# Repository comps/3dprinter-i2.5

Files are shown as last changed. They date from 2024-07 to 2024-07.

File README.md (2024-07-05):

# The i2.5 ("Tiny") 3D printer

This was a learning project of mine on how to design and build a moving-bed
style 3D printer from scratch.

It started in ~2017 and grew in time and money spent from there, with me trying
various "new technologies" on the always-work-in-progress printer.

Things like

- sliding IGUS bushings instead of LM8UU bearings
- graphite-based self-lubricating brass bushings instead of LM8UU
- grease types on the Z-axis screw (dry graphite/teflon, calcium sulfonate,
  etc.)
- belt tensioning systems (and various types of timing belt fiber
  reinforcements)
- Z-axis screw couplers and their (in)accuracy
- bed probing (the design has left-over space for an X-gantry-mounted
  limit switch probe, the real printer ended up using an X-carriage
  inductive probe)
- inductive probe options and failure modes (~4 variants, sensors randomly
  failing due to 60C heat from the bed)
- magnetic beds and their limitations (tried 2-3 variants, some DIY,
  some purchased)
  - ended up using bed clamps as discrete magnets (glued to underside)
    were never strong enough to prevent the steel sheet from moving
  - sourcing spring steel sheets was also near-impossible in 2019
- heated bed issues (tried PCB, which flexed too much, tried fixing
  aluminium heatbed with broken corners, reliability issues, etc.)
  - also several variations on bed springs (stiffness, types, ended up
    with silicone-based springs)
- electronics
  - started as 8-bit, two different boards, using custom wiring
    for TMC2130 back when it was bleeding-edge and only Prusa had it
  - added an 8x8 red LED matrix to show gcode command queue
  - developed custom Blue Pill based stack for a 32bit cut-down Marlin 2.0
  - switched to a stock imported 32bit board later on
- extruder was originally a custom design loosely based on Greg's Wade's
  geared extruder using E3D V6, then re-worked to use E3D Titan Aero heatsink,
  then abandoned for a stock E3D Titan Aero extruder
  - with a custom-modified NEMA17 motor to use a longer shaft, so it can be
    mounted through the X-carriage, distributing front/back weight

Ultimately, the scope and cost of the project ended up being about 10x of what
it was originally meant to be, mainly thanks to unreliable, out-of-spec and
otherwise broken parts from Ebay and Aliexpress.  
(Bearings binding, bushings with wrong hole tolerances, electronics randomly
failing, IC chips like CH340 randomly locking up, toothed gears for driving
filament being made of soft metal, GT2 pulleys with malformed teeth, etc., etc.)

This repository therefore serves mainly as a source of spare parts for the one
printer that was ever built.

Please don't build another one, there are many better options these days.  
It's not 2017 anymore.

---

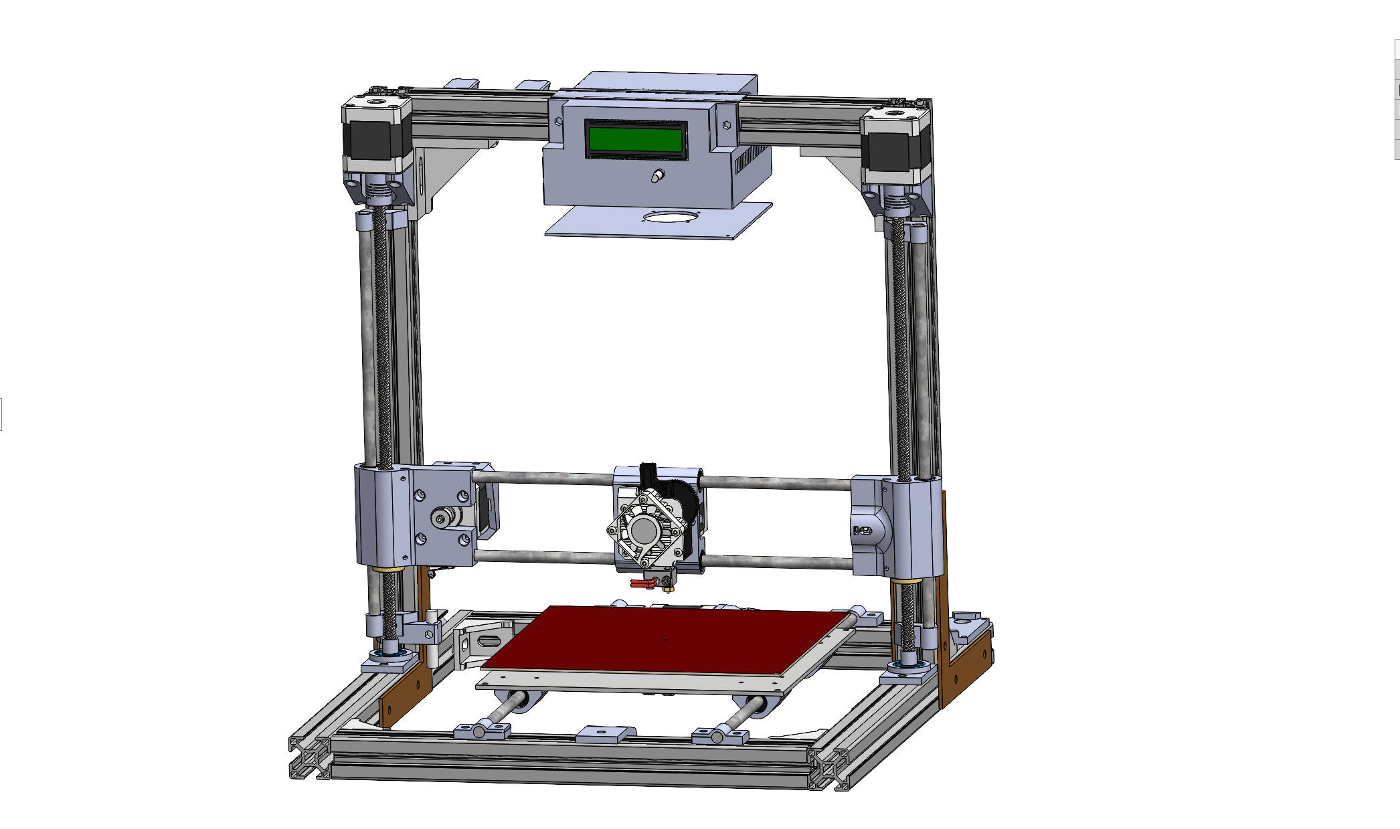
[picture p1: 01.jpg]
front overview

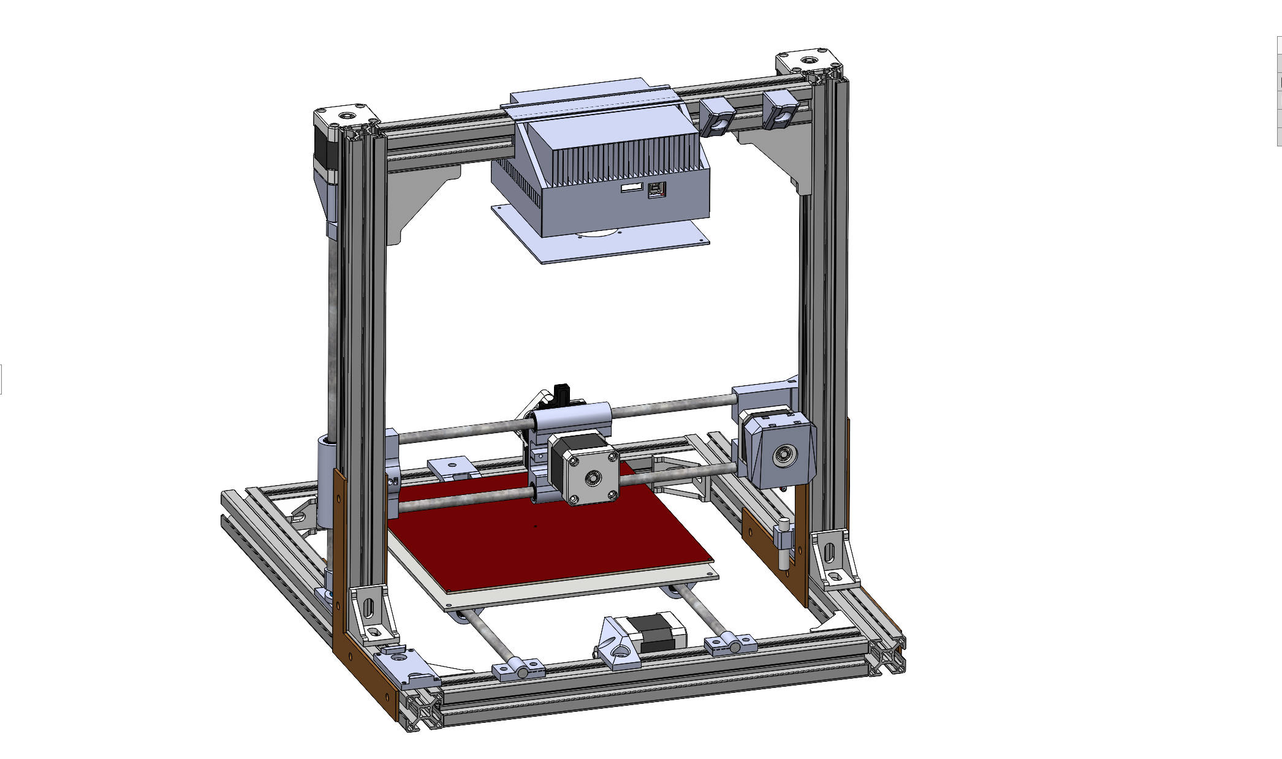
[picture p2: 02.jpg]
back overview

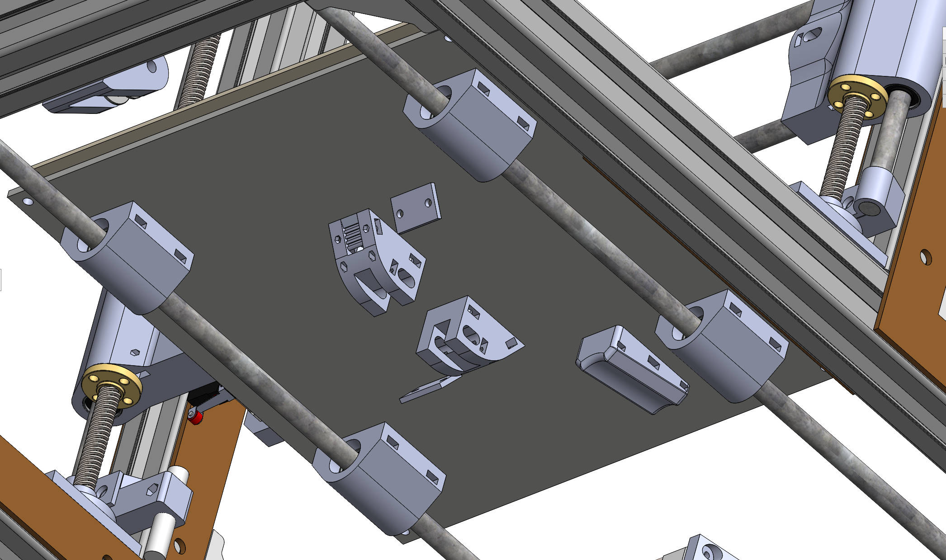
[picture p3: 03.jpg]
underside


---

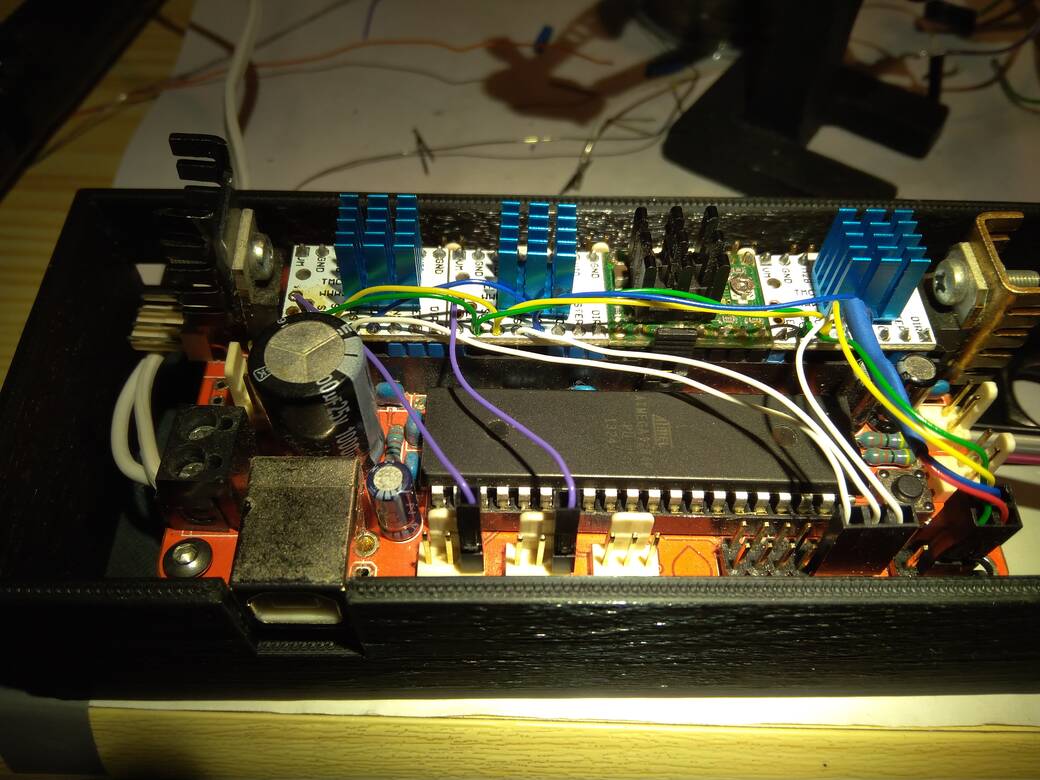
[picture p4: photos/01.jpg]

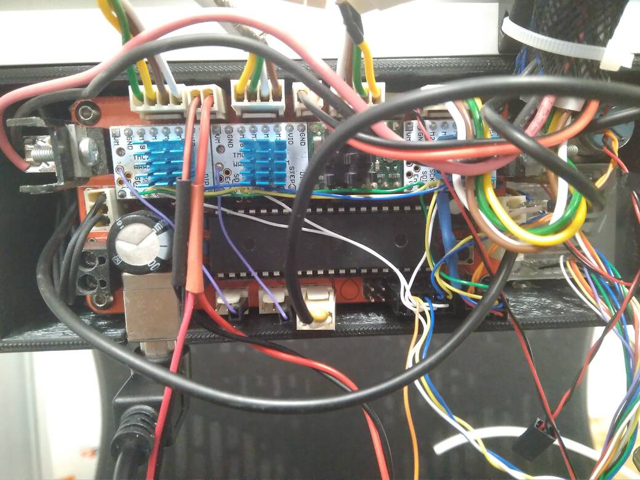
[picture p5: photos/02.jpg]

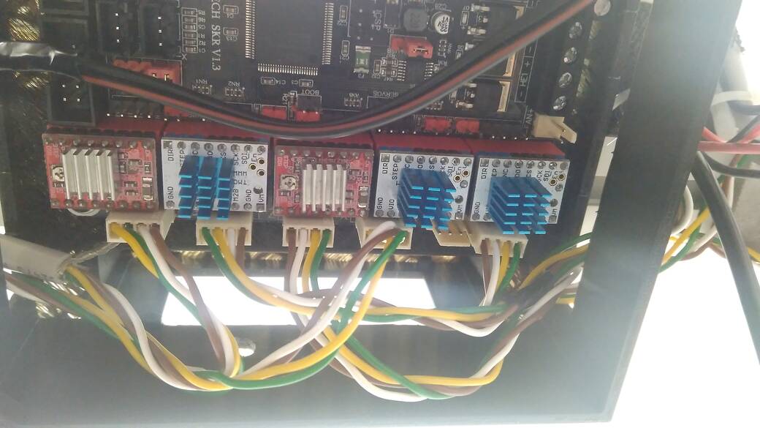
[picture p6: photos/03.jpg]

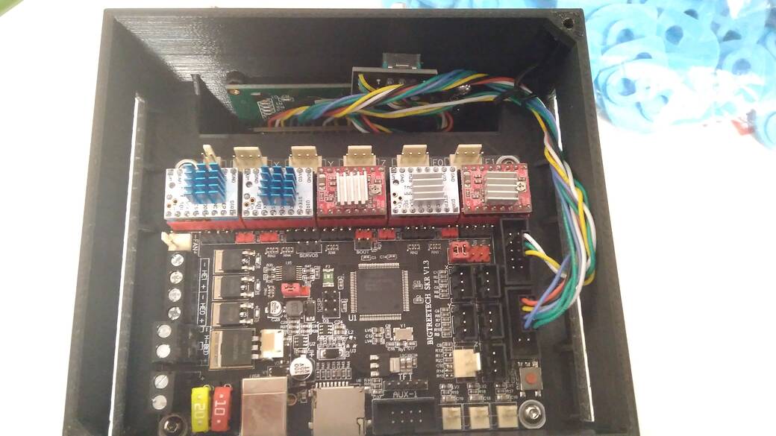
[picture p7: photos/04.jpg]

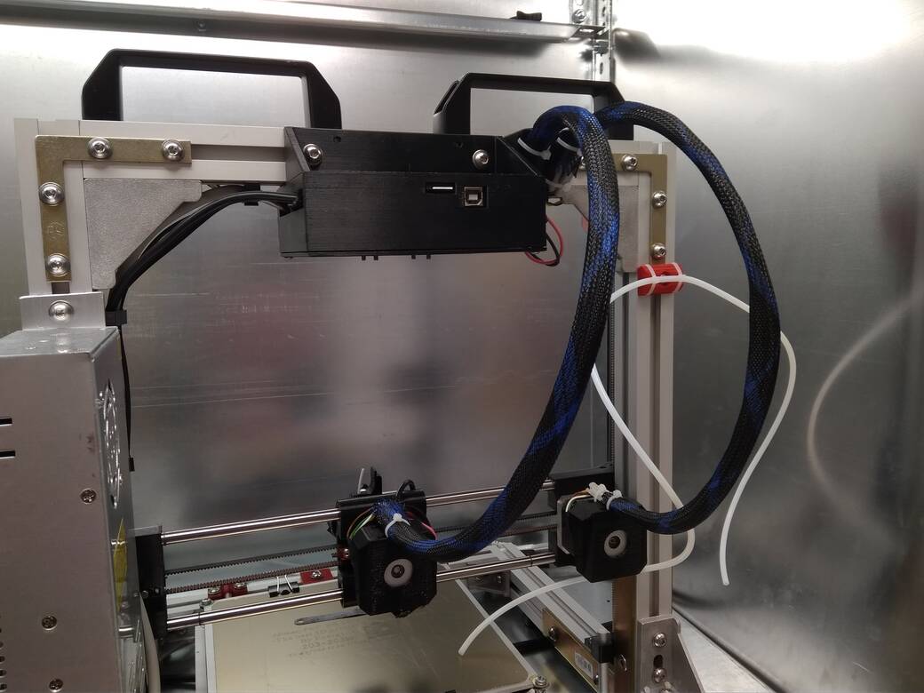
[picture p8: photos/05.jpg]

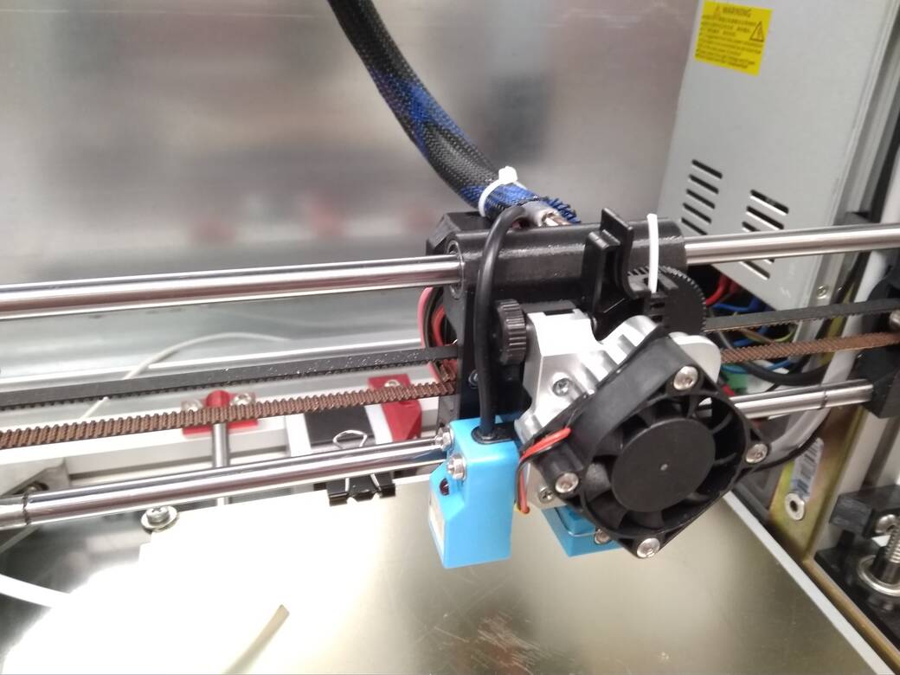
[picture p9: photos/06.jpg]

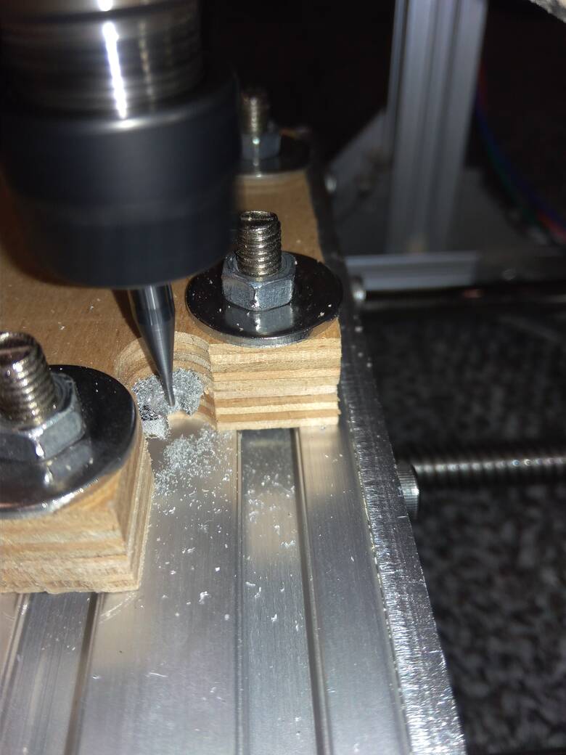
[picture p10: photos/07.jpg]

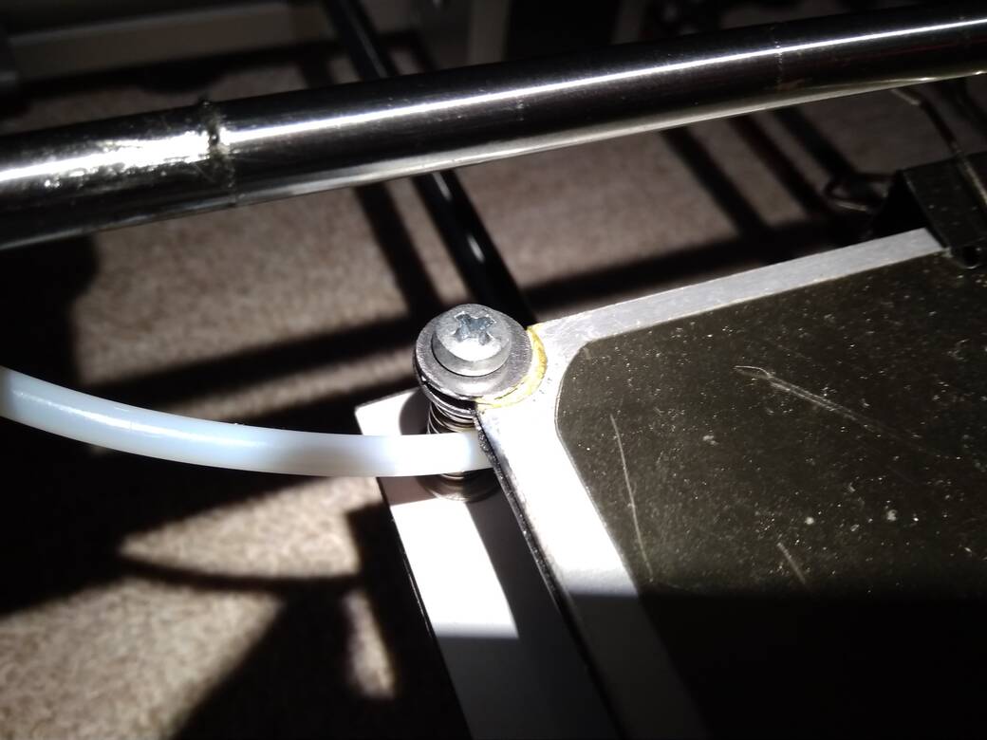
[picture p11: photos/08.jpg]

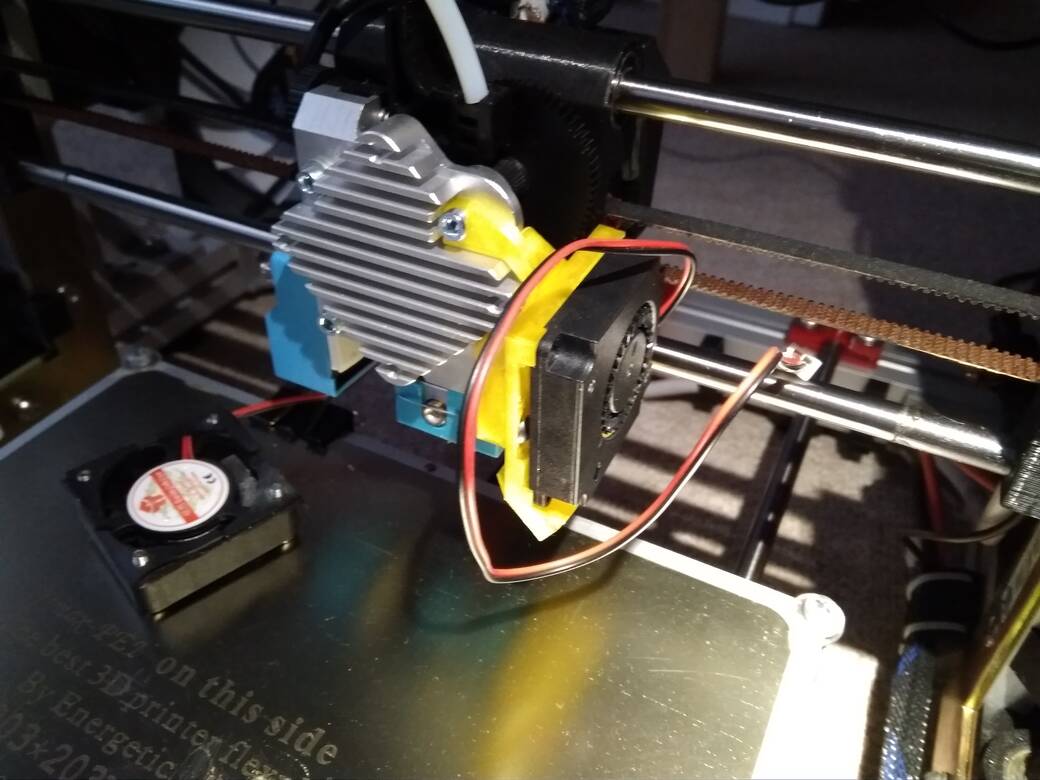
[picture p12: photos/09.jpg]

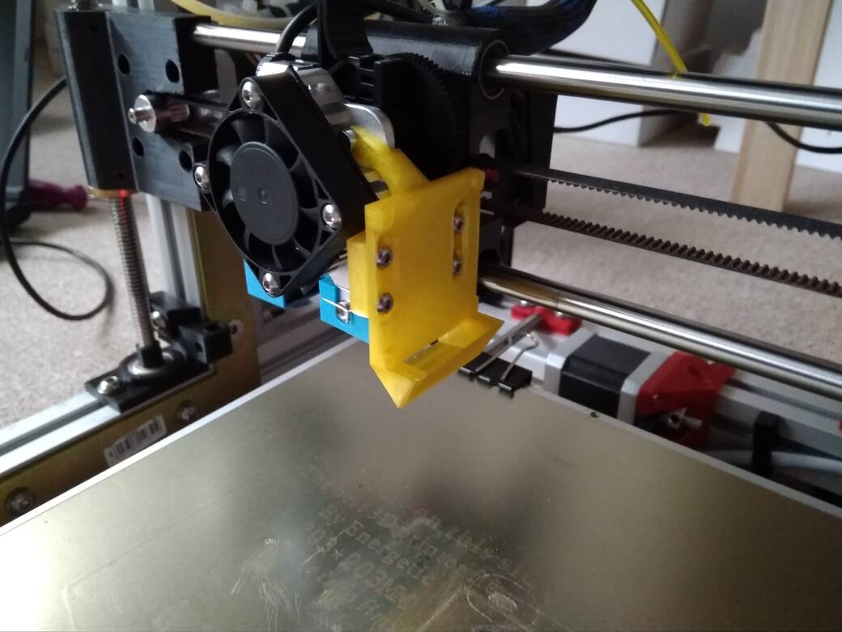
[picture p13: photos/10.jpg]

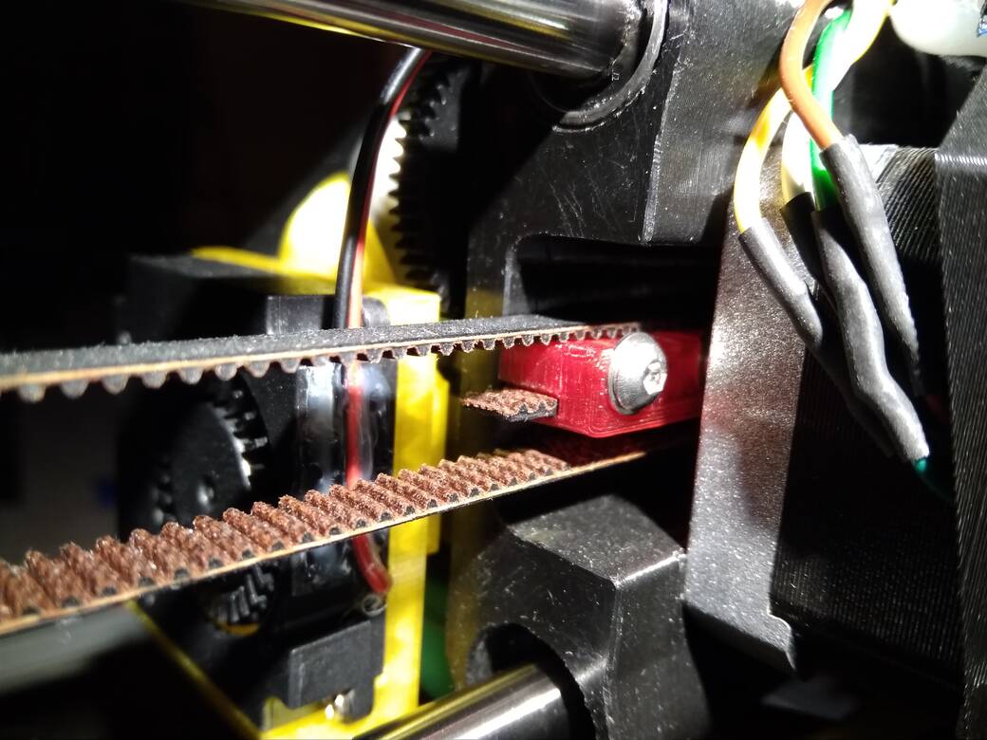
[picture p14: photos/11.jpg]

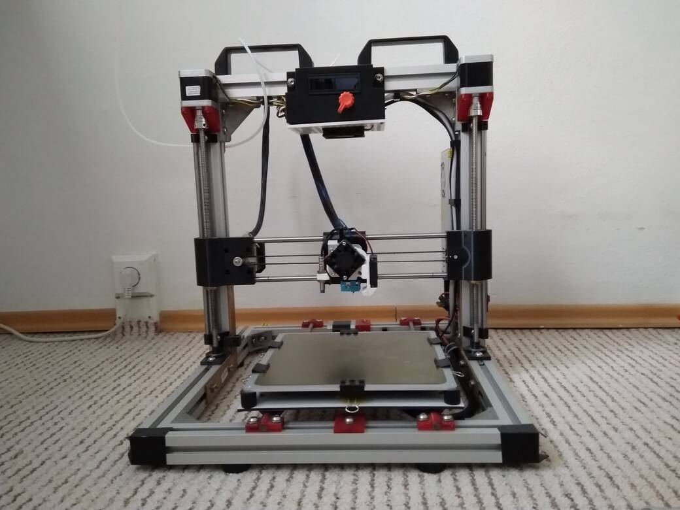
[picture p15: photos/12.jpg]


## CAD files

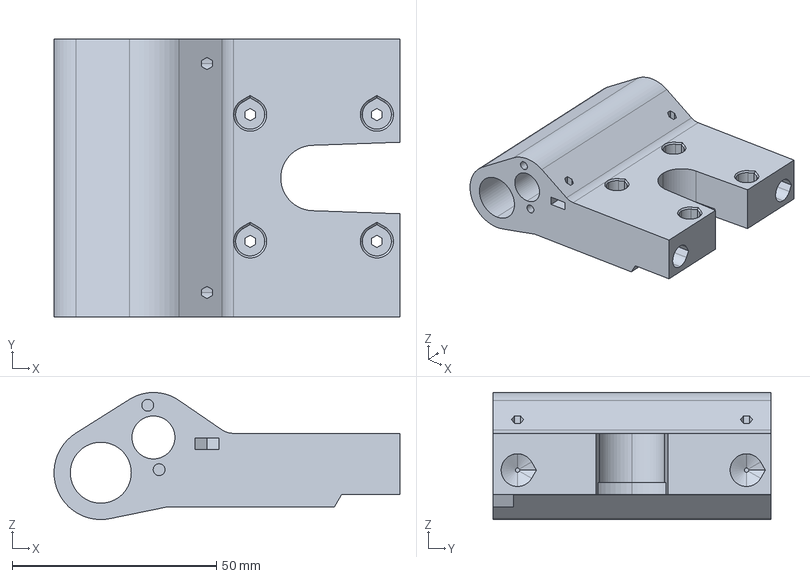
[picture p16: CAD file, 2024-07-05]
x-axis-holders-left.STEP
84.6 x 68.0 x 31.1 mm

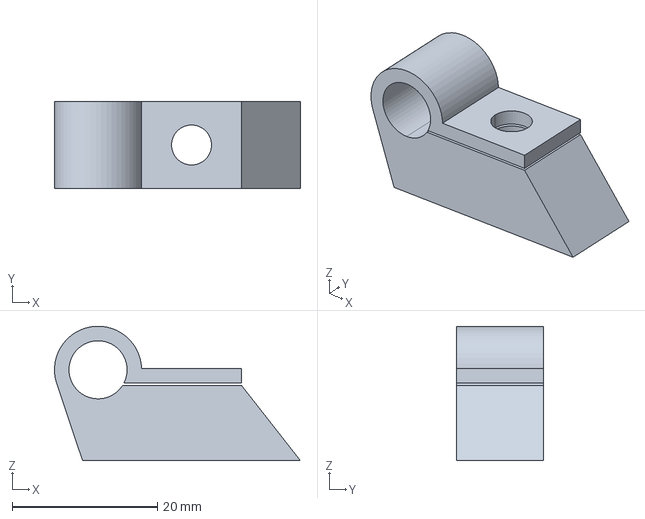
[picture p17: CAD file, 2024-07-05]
z-rod-holders-top.STEP
33.9 x 12.0 x 18.5 mm

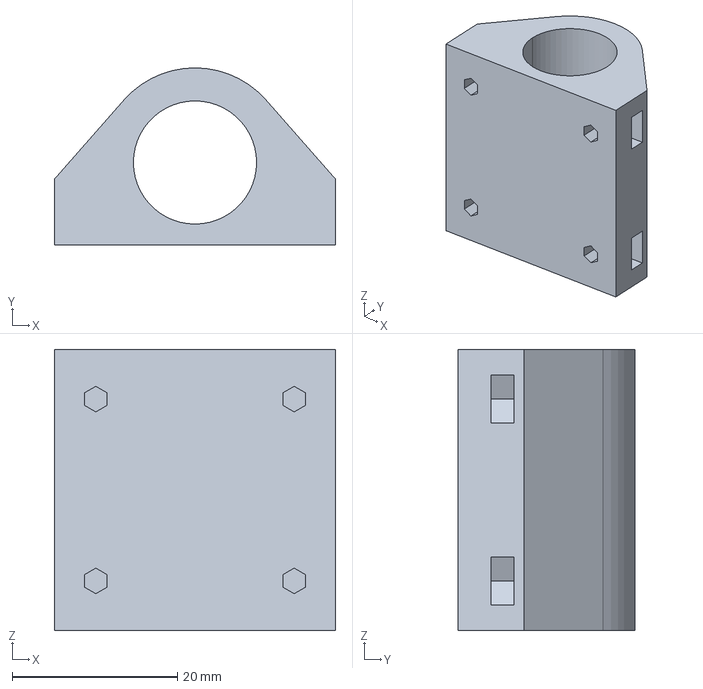
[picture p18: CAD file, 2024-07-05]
y-lm8uu-holder.STEP
34.0 x 21.5 x 34.0 mm

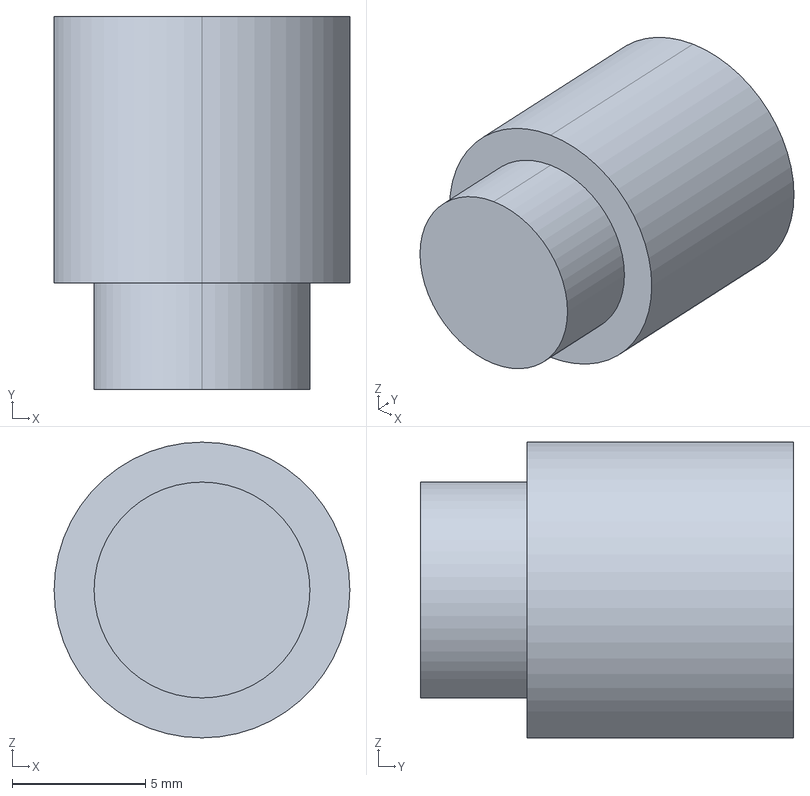
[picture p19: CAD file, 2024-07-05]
z-rod-support-sock.STEP
11.1 x 14.0 x 11.1 mm

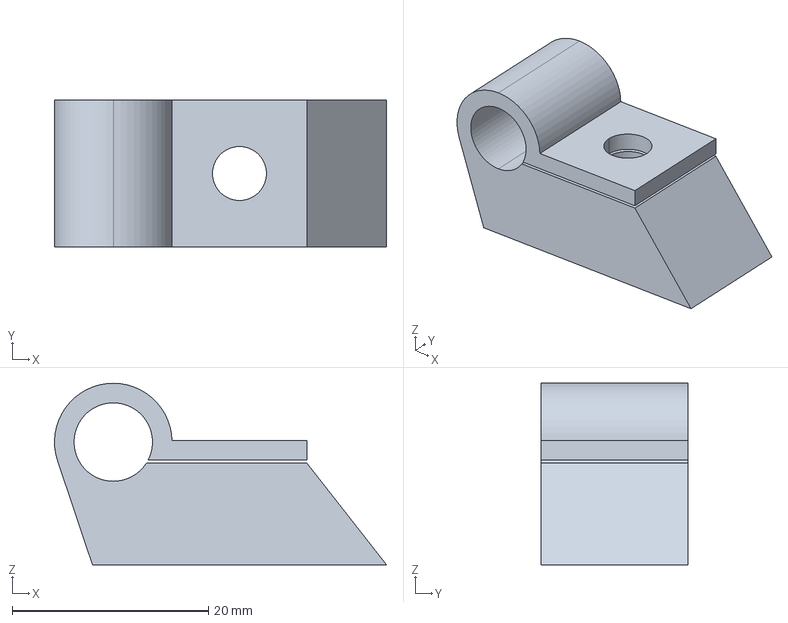
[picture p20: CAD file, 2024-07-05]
z-rod-holders-bottom.STEP
33.9 x 15.0 x 18.5 mm

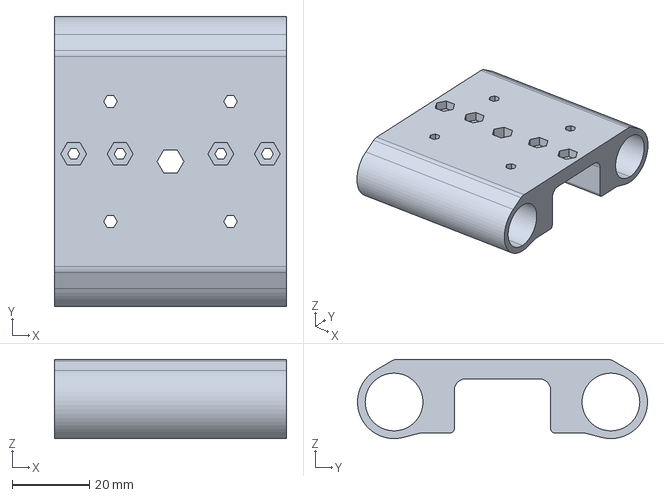
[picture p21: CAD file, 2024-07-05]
x-carriage.STEP
60.0 x 74.9 x 20.4 mm

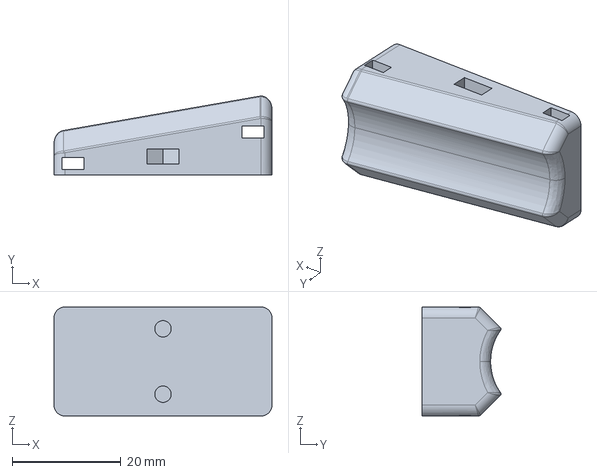
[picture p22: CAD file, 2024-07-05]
y-bed-wire-support-carriage.STEP
40.0 x 14.5 x 20.0 mm

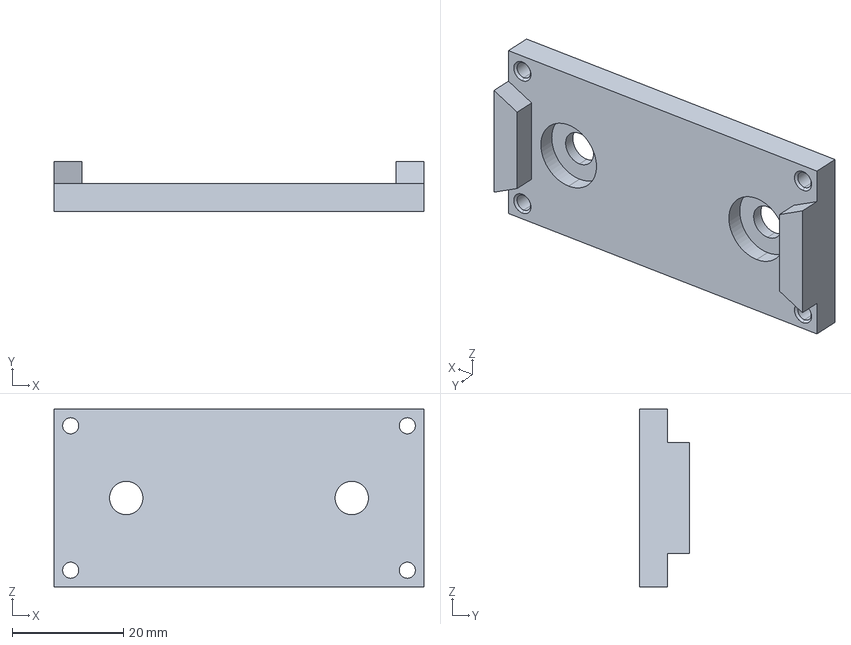
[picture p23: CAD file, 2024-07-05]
bed-mosfet-base.STEP
66.6 x 9.00 x 32.0 mm

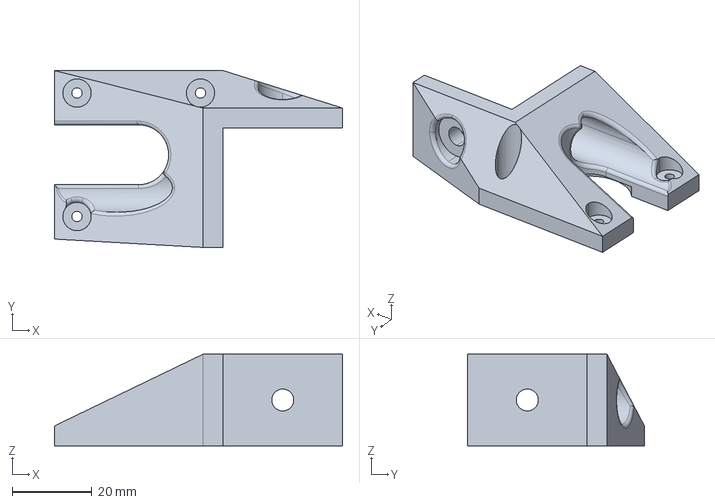
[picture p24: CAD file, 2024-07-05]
y-stepper-holder.STEP
72.3 x 44.4 x 23.0 mm

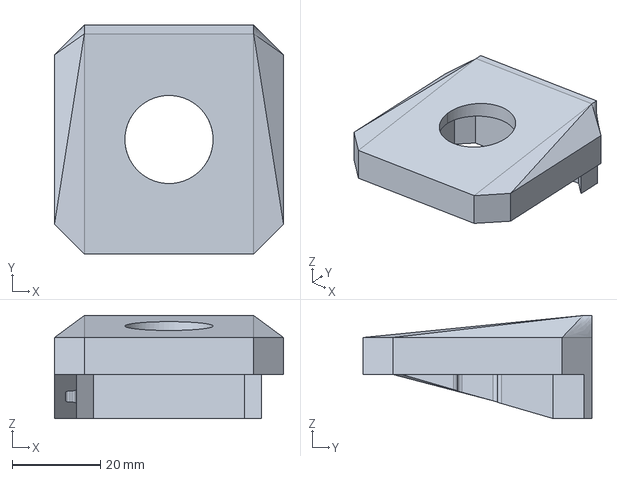
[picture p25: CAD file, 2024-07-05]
x-wire-support-nema17.STEP
52.0 x 52.0 x 23.4 mm

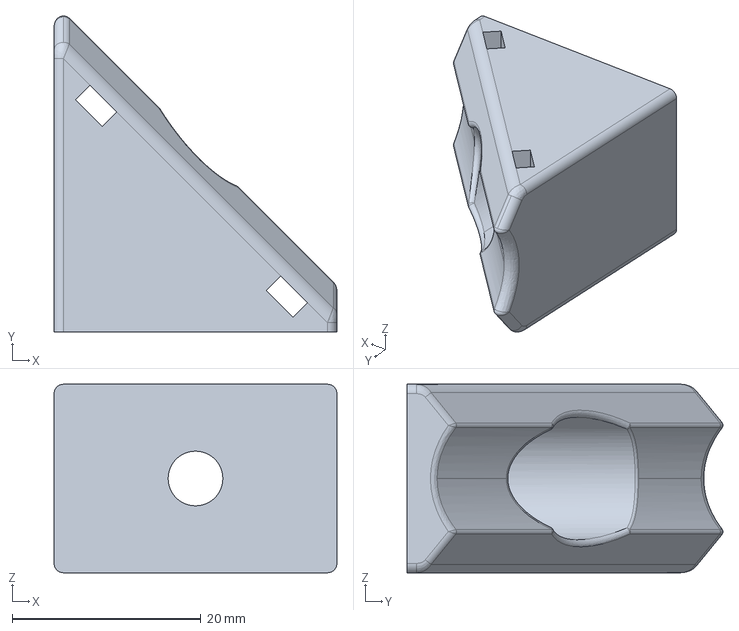
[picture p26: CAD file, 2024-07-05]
x-top-wire-support.STEP
30.0 x 33.5 x 20.0 mm

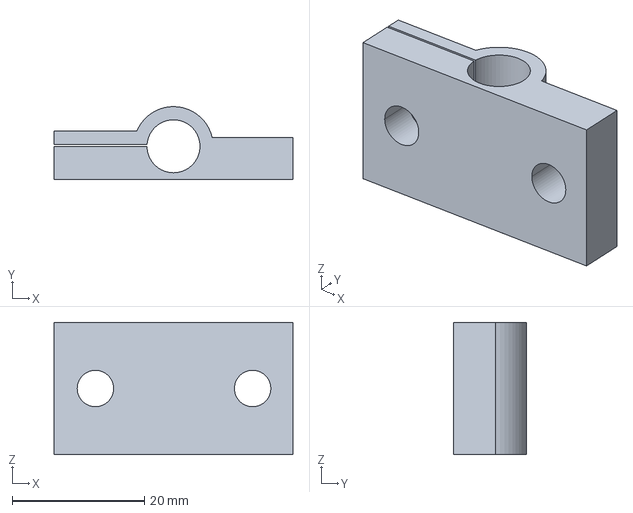
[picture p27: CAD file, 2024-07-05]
y-rod-holder.STEP
36.1 x 11.0 x 20.0 mm

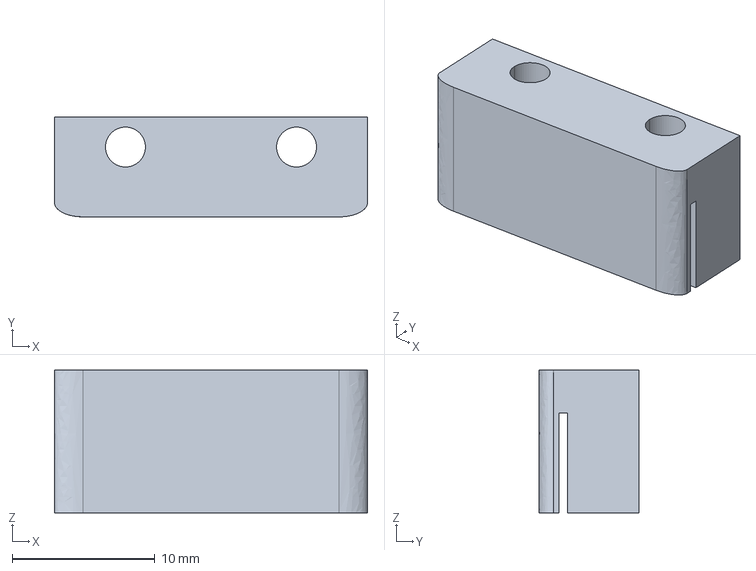
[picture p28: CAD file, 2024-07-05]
x-carriage-belt-holder-right.STEP
22.0 x 7.00 x 10.0 mm

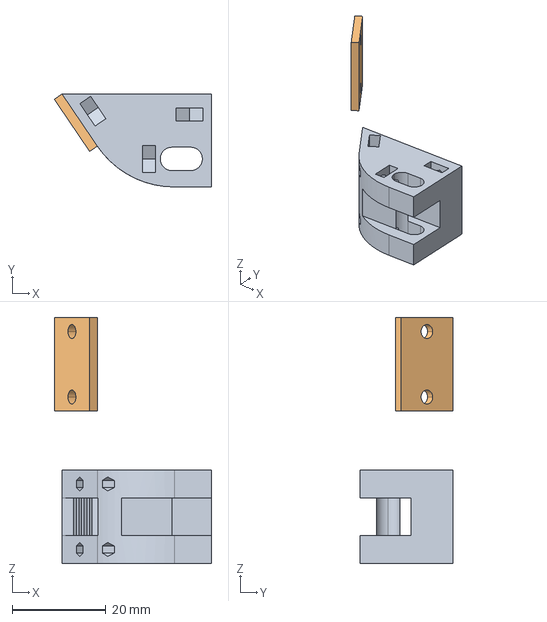
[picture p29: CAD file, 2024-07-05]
y-carriage-belt-holder.STEP
33.7 x 19.9 x 52.6 mm

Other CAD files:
x-carriage-belt-holder-left.STEP
y-idler-holder.STEP
z-stepper-holder.STEP
32bit-box-base.STEP
x-axis-holders-right.STEP
z-rod-holders-bottom-zscrew.STEP
z-rod-support-boot.STEP
